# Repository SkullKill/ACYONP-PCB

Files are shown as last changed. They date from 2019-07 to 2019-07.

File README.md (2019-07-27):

# ACYONP-PCB
PCB for Access Control Yubikey OTP NFC Pi (ACYONP). For Raspberry Pi. This is a **Door Access Control using Electronic Door Strike, with Yubikey OTP via NFC / KeyPad / WebInterface for Authentication.**

Web interface shows the status of the whole system, along with the ability to enter pin/password/yubikey OTP string for authentication to unlock the door

Uses Inturrupt and Threads to minimise overhead, and to be non blocking as much as possible.

All options are completely customizable through the ini config file

The script [ACYONP](https://github.com/SkullKill/ACYONP) is design specificly for the Raspberry Pi.

SKaccess by Simon Kong

https://www.skaccess.com

ACYONP-SMD-01.jpg
NFC Reader is at the top of the Box, inside. putting the yubikey on top of the box will scan the yubikey neo / yubikey 5 nfc.


ACYONP-webinterface-01.jpg


## V 1.0 21/05/2019 - Initial Release

  ------------------------------------------------------------
## PCB Board Used

Ready to use PCB Board

https://www.skstore.com.au/electronics/pcb/ACYONP

PCB Design Files / gerber files

[ACYONP-PCB](https://github.com/SkullKill/ACYONP-PCB)

FYI Gerber files are in the release section

https://github.com/SkullKill/ACYONP-PCB/releases

more pictures in the wiki

https://github.com/SkullKill/ACYONP-PCB/wiki

ACYONP-SMD-Front-Red-RT-V1.2.jpg


ACYONP-SMD-Back-Red-V1.2.jpg


  ------------------------------------------------------------
## Schematics

ACYONP-SMD-schematics-v1.2a.jpg


------------------------------------------------------------
## Code Used

[ACYONP](https://github.com/SkullKill/ACYONP)

------------------------------------------------------------
## Product Used (not included)

### Dupont kit / Jumper Wires
you will need a dupont crimp kit 2.54 / tool
and / or jumper wires

e.g

Crimping Tool: 0.1-1.0 mm² Capacity, 16-28 AWG
https://www.pololu.com/product/1928

Crimp Connector Housings
https://www.pololu.com/category/70/crimp-connector-housings

Female Crimp Pins for 0.1" Housings
https://www.pololu.com/product/1930

Male Crimp Pins for 0.1" Housings
https://www.pololu.com/product/1931

Wires with Pre-Crimped Terminals
https://www.pololu.com/category/71/wires-with-pre-crimped-terminals

Premium Jumper Wires
https://www.pololu.com/category/65/premium-jumper-wires

https://www.futurlec.com/ConnHead.shtml

### Keypad

Metallic Waterproof 3x4 Keypad
https://www.futurlec.com/Keypads.shtml

### PN532 NFC controller in UART mode

e.g

https://www.dfrobot.com/product-892.html

https://wiki.dfrobot.com/NFC_Module_for_Arduino__SKU_DFR0231_

### Yubico Yubikey
YubiKey 5 NFC

https://www.yubico.com/product/yubikey-5-nfc

### other items used, can be any other ones.

H0307 • 145Lx105Wx65Dmm IP65 Sealed ABS Enclosure

https://www.altronics.com.au/p/h0307-ritec-145lx105wx65dmm-ip65-sealed-abs-enclosure/

H0151 • UB1 (157Lx95Wx53Hmm) Grey ABS Jiffy Box

https://www.altronics.com.au/p/h0151-ub1-157lx95wx53hmm-grey-abs-jiffy-box/

P0628 • 2.1mm Female Plastic Chassis Mount DC Power Socket (not necessary)

https://www.altronics.com.au/p/p0628-2.1mm-female-plastic-chassis-mount-dc-power-socket/

H1554 • 5mm LED Mounts Pk 100

https://www.altronics.com.au/p/h1554-5mm-led-mounts-pk-100/

S6109 • 1.5-24V Piezo Chassis Mount Buzzer (status buzzer)

https://www.altronics.com.au/p/s6109-1.5-24v-piezo-chassis-mount-buzzer/

S6100 • 3-15V Mechanical Chassis Mount Buzzer (door buzzer)

https://www.altronics.com.au/p/s6100-3-15v-mechanical-chassis-mount-buzzer/

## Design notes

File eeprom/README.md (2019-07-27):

https://github.com/raspberrypi/hats/tree/master/eepromutils

https://github.com/raspberrypi/linux/tree/rpi-4.19.y/arch/arm/boot/dts/overlays

https://www.stderr.nl/Blog/Hardware/RaspberryPi/PowerButton.html

https://lb.raspberrypi.org/forums/viewtopic.php?t=108134

vi /boot/config.txt
dtparam=i2c_vc=on

git clone https://github.com/raspberrypi/hats.git
sudo apt-get install device-tree-compiler

./eepmake eeprom_settings.txt acyonp_hat.eep

dd if=/dev/zero ibs=1k count=4 of=blank.eep

hexdump blank.eep

sudo ./eepflash.sh -w -f=blank.eep -t=24c32

sudo hexdump /sys/class/i2c-adapter/i2c-0/0-0050/eeprom

sudo ./eepflash.sh -w -f=acyonp_hat.eep -t=24c32

cat /proc/device-tree/hat/vendor
cat /proc/device-tree/hat/product

sudo sh -c 'echo "18" > /sys/class/gpio/export'
sudo sh -c 'echo "out" > /sys/class/gpio/gpio18/direction'
sudo sh -c 'echo "1" > /sys/class/gpio/gpio18/value'
sudo sh -c 'echo "0" > /sys/class/gpio/gpio18/value'

# compile dts overlay 
sudo dtc -@ -I dts -O dtb -o pi3-miniuart-bt-w1-gpio-overlay.dtb pi3-miniuart-bt-w1-gpio-overlay.dts ; sudo chown pi:pi pi3-miniuart-bt-w1-gpio-overlay.dtb

fdtdump pi3-miniuart-bt-w1-gpio-overlay.dtb

# generate eep with both board definition, and device-tree
./eepmake eeprom_settings.txt acyonp_hat-with-dt.eep pi3-miniuart-bt-w1-gpio-overlay.dtb

sudo ./eepflash.sh -w -f=blank.eep -t=24c32
sudo ./eepflash.sh -w -f=acyonp_hat-with-dt.eep -t=24c32

hexdump acyonp_hat-with-dt.eep
sudo hexdump /sys/class/i2c-adapter/i2c-0/0-0050/eeprom

To allow auto configuration after kernel boot (ie: modprobe some modules, TFT calibration, etc...), I use a custom parameter file, based on JSON, that could be parsed after. I choose JSON as it is small, human-readable, and easy to parse.
To add a custom file to your eep, just do this:
Code: Select all

./eepmake eeprom_settings.txt acyonp_hat-with-dt.eep myled.dtb -c myparams.json

cat /proc/device-tree/hat/product
cat /proc/device-tree/hat/product_id
cat /proc/device-tree/hat/product_ver
cat /proc/device-tree/hat/uuid
cat /proc/device-tree/hat/vendor

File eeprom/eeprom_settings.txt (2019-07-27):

########################################################################
# EEPROM settings text file
#
# Edit this file for your particular board and run through eepmake tool,
# then use eepflash tool to write to attached HAT ID EEPROM 
#
# Tools available:
#  eepmake   Parses EEPROM text file and creates binary .eep file
#  eepdump   Dumps a binary .eep file as human readable text (for debug)
#  eepflash  Write or read .eep binary image to/from HAT EEPROM
#
########################################################################

########################################################################
# Vendor info

# 128 bit UUID. If left at zero eepmake tool will auto-generate
# RFC 4122 compliant UUID
product_uuid 00000000-0000-0000-0000-000000000000

# 16 bit product id
product_id 0x0001

# 16 bit product version
product_ver 0x0001

# ASCII vendor string  (max 255 characters)
vendor "SKaccess"

# ASCII product string (max 255 characters)
product "ACYONP - Access Control Yubikey OTP NFC Pi"

########################################################################
# GPIO bank settings, set to nonzero to change from the default.
# NOTE these setting can only be set per BANK, uncommenting any of
# these will force the bank to use the custom setting.

# drive strength, 0=default, 1-8=2,4,6,8,10,12,14,16mA, 9-15=reserved
gpio_drive 0

# 0=default, 1=slew rate limiting, 2=no slew limiting, 3=reserved
gpio_slew 0

# 0=default, 1=hysteresis disabled, 2=hysteresis enabled, 3=reserved
gpio_hysteresis 0

# If board back-powers Pi via 5V GPIO header pins:
# 0 = board does not back-power
# 1 = board back-powers and can supply the Pi with a minimum of 1.3A
# 2 = board back-powers and can supply the Pi with a minimum of 2A
# 3 = reserved
# If back_power=2 then USB high current mode will be automatically 
# enabled on the Pi
back_power 2

########################################################################
# GPIO pins, uncomment for GPIOs used on board
# Options for FUNCTION: INPUT, OUTPUT, ALT0-ALT5
# Options for PULL: DEFAULT, UP, DOWN, NONE
# NB GPIO0 and GPIO1 are reserved for ID EEPROM so cannot be set

#         GPIO  FUNCTION  PULL
#         ----  --------  ----
#setgpio  2     INPUT     DEFAULT
#setgpio  3     INPUT     DEFAULT
#setgpio  4     INPUT     DEFAULT
#setgpio  5     INPUT     DEFAULT
#setgpio  6     INPUT     DEFAULT
#setgpio  7     INPUT     DEFAULT
#setgpio  8     INPUT     DEFAULT
#setgpio  9     INPUT     DEFAULT
#setgpio  10    INPUT     DEFAULT
#setgpio  11    INPUT     DEFAULT
#setgpio  12    INPUT     DEFAULT
#setgpio  13    INPUT     DEFAULT
#setgpio  14    INPUT     DEFAULT
#setgpio  15    INPUT     DEFAULT
#setgpio  16    INPUT     DEFAULT
#setgpio  17    INPUT     DEFAULT
#setgpio  18    INPUT     DEFAULT
#setgpio  19    INPUT     DEFAULT
#setgpio  20    INPUT     DEFAULT
#setgpio  21    INPUT     DEFAULT
#setgpio  22    INPUT     DEFAULT
#setgpio  23    INPUT     DEFAULT
#setgpio  24    INPUT     DEFAULT
#setgpio  25    INPUT     DEFAULT
#setgpio  26    INPUT     DEFAULT
#setgpio  27    INPUT     DEFAULT

#         GPIO  FUNCTION  PULL
#         ----  --------  ----
# unused / KeyPad Col 4 / i2c SDA
#setgpio  2     INPUT     DEFAULT
# Relay 4 / i2c SCL
#setgpio  3     OUTPUT     DOWN
# 1-wire
#setgpio  4     INPUT     DEFAULT
# Power to Solenoid strike input
setgpio  5     INPUT     UP
# Latch Open input
setgpio  6     INPUT     UP
# Relay 3
setgpio  7     OUTPUT     DOWN
# Relay 2 Door Buzzer
setgpio  8     OUTPUT     DOWN
# KeyPad Col 3
setgpio  9     OUTPUT     DOWN
# KeyPad Col 2
setgpio  10    OUTPUT     DOWN
# Relay 1 Door Strike
setgpio  11    OUTPUT     DOWN
# Reed Switch Open input
setgpio  12    INPUT     UP
# DoorOpen Button
setgpio  13    INPUT     UP
# To NFC TX
setgpio  14    ALT0     DEFAULT
# to NFC RX
setgpio  15    ALT0     DEFAULT
# Latch Open LED
setgpio  16    OUTPUT     DOWN
# KeyPad Row 1
setgpio  17    INPUT     UP
# PWM status buzzer (active, not passive, so no PWM used)
setgpio  18    OUTPUT     DOWN
# Power to Solenoid Strike LED
setgpio  19    OUTPUT     DOWN
# Alarm LED
setgpio  20    OUTPUT     DOWN
# Status LED
setgpio  21    OUTPUT     DOWN
# KeyPad Row 3
setgpio  22    INPUT     UP
# KeyPad Row 4
setgpio  23    INPUT     UP
# KeyPad Col 1
setgpio  24    OUTPUT     DOWN
# NFC PowerSwitch
setgpio  25    OUTPUT     DOWN
# Reed Switch open LED
setgpio  26    OUTPUT     DOWN
# KeyPad Row 2
setgpio  27    INPUT     UP

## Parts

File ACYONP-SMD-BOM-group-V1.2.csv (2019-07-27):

Reference | Quantity | Value | Footprint | Datasheet | LCSC | LCSCweb | ALT | MPN | Alt | MPNweb | web
C2 C5 C3 C6 | 4 | 100nF-25V | Capacitor_SMD:C_0805_2012Metric_Pad1.15x1.40mm_HandSolder | https://datasheet.lcsc.com/szlcsc/Murata-Electronics-GRM21BR71E104KA01L_C86041.pdf | C86041 | https://lcsc.com/product-detail/Multilayer-Ceramic-Capacitors-MLCC-SMD-SMT_MuRata_GRM21BR71E104KA01L_100nF-104-10-25V_C86041.html |  | GRM21BR71E104KA01L
C4 C1 C7 | 3 | 22UF-25V | Capacitor_SMD:C_0805_2012Metric_Pad1.15x1.40mm_HandSolder | https://datasheet.lcsc.com/szlcsc/Samsung-Electro-Mechanics-CL21A226MAQNNNE_C45783.pdf | C45783 | https://lcsc.com/product-detail/Multilayer-Ceramic-Capacitors-MLCC-SMD-SMT_SAMSUNG_CL21A226MAQNNNE_22uF-226-20-25V_C45783.html | C86816 | CL21A226MAQNNNE
D1 D10 D9 D2 | 4 | SOD1F7 | Diode_SMD:D_SOD-123 | https://datasheet.lcsc.com/szlcsc/1903041730_MDD-Jiangsu-Yutai-Elec-SOD1F7_C33221.pdf | C33221 | https://lcsc.com/product-detail/Diodes-Rectifiers-Fast-Recovery_Jiangsu-Yutai-Elec-SOD1F7_C33221.html |  | SOD1F7
D3 D4 D11 D12 D13 D14 D15 | 7 | LED-Green | LED_SMD:LED_0805_2012Metric_Pad1.15x1.40mm_HandSolder | https://datasheet.lcsc.com/szlcsc/Foshan-NationStar-Optoelectronics-FC-2012UGK-520D5_C84260.pdf | C84260 | https://lcsc.com/product-detail/Light-Emitting-Diodes-LED_Emerald-SMDLED-Iv-220-270mcd-atIF-5mA_C84260.html |  | FC-2012UGK-520D5
D5 D6 | 2 | LED-Yellow | LED_SMD:LED_0805_2012Metric_Pad1.15x1.40mm_HandSolder | https://datasheet.lcsc.com/szlcsc/Foshan-NationStar-Optoelectronics-FC-2012HYK-588J_C84261.pdf | C84261 | https://lcsc.com/product-detail/Light-Emitting-Diodes-LED_Yellow-light-SMDLED-105-125mcd_C84261.html |  | FC-2012HYK-588J
D7 | 1 | LED-Red | LED_SMD:LED_0805_2012Metric_Pad1.15x1.40mm_HandSolder | https://datasheet.lcsc.com/szlcsc/Foshan-NationStar-Optoelectronics-FC-2012HRK-620D_C84256.pdf | C84256 | https://lcsc.com/product-detail/Light-Emitting-Diodes-LED_Red-LED-SMDLED-80-180mcd_C84256.html |  | FC-2012HRK-620D
D8 | 1 | LED-Blue | LED_SMD:LED_0805_2012Metric_Pad1.15x1.40mm_HandSolder | https://datasheet.lcsc.com/szlcsc/Foshan-NationStar-Optoelectronics-FC-A2012BK-470H2_C84259.pdf | C84259 | https://lcsc.com/product-detail/Light-Emitting-Diodes-LED_Blue-light-SMDLED-36-45mcdat2mA_C84259.html |  | FC-A2012BK-470H2
F1 | 1 | PTC-2A-16V_1812 | Fuse:Fuse_1812_4532Metric_Pad1.30x3.40mm_HandSolder | https://datasheet.lcsc.com/szlcsc/SOCAY-Elec-SCF200-16-1812R_C305617.pdf | C305617 | https://lcsc.com/product-detail/Others_SOCAY-Elec-SCF200-16-1812R_C305617.html |  | SCF200-16-1812R
J1 | 1 | Raspberry_Pi_2_3 | Connector_PinSocket_2.54mm:PinSocket_2x20_P2.54mm_Vertical | https://www.raspberrypi.org/documentation/hardware/raspberrypi/schematics/rpi_SCH_3bplus_1p0_reduced.pdf | C50982 | https://lcsc.com/product-detail/Pin-Header-Female-Header_Boom-Precision-Elec-2-54mm-2-20PFemale-header_C50982.html |  |  | C35165
J12 | 1 | 1-Wire | Connector_PinHeader_2.54mm:PinHeader_1x03_P2.54mm_Vertical | https://datasheet.lcsc.com/szlcsc/Boom-Precision-Elec-Header-2-54mm-1-3P_C49257.pdf | C49257 | https://lcsc.com/product-detail/Pin-Header-Female-Header_Boom-Precision-Elec-Header-2-54mm-1-3P_C49257.html
J15 | 1 | NFC_Module | Connector_PinHeader_2.54mm:PinHeader_1x04_P2.54mm_Vertical | https://datasheet.lcsc.com/szlcsc/Shenzhen-Cankemeng-Headers-Pins-1-4P-2-54mm-Straight-line_C124378.pdf | C124378 | https://lcsc.com/product-detail/Pin-Header-Female-Header_Shenzhen-Cankemeng-Headers-Pins-1-4P-2-54mm-Straight-line_C124378.html
J16 | 1 | 12Vpsu | TerminalBlock:TerminalBlock_bornier-2_P5.08mm | https://datasheet.lcsc.com/szlcsc/Ningbo-Kangnex-Elec-WJ126V-5-0-2P_C8404.pdf | C8404 | https://lcsc.com/product-detail/Pluggable-System-Terminal-Block_Ningbo-Kangnex-Elec-WJ126V-5-0-2P_C8404.html |  | WJ126V-5.0-2P
J18 | 1 | LatchOpen | Connector_PinHeader_2.54mm:PinHeader_1x02_P2.54mm_Vertical | ~ | C124375
J19 | 1 | ReedSwitchOpen | Connector_PinHeader_2.54mm:PinHeader_1x02_P2.54mm_Vertical | ~ | C124375
J20 | 1 | AlarmStatus | Connector_PinHeader_2.54mm:PinHeader_1x02_P2.54mm_Vertical | ~ | C124375
J21 | 1 | PowerStatus | Connector_PinHeader_2.54mm:PinHeader_1x02_P2.54mm_Vertical | ~ | C124375
J22 | 1 | ProgrammingJumper | Connector_PinHeader_2.54mm:PinHeader_1x02_P2.54mm_Vertical | ~ | C124375
J23 | 1 | Screw_Terminal_01x04_Left_Top | TerminalBlock_TE-Connectivity:TerminalBlock_TE_282834-4_1x04_P2.54mm_Horizontal | ~ |  |  |  | KF128-2.54-4P |  | http://en.cnkefa.com/index.php?c=product&id=159 | https://www.aliexpress.com/store/group/Connection-terminal/4657016_515213135.html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
J24 | 1 | Screw_Terminal_01x04_Left_Bottom | TerminalBlock_TE-Connectivity:TerminalBlock_TE_282834-4_1x04_P2.54mm_Horizontal | ~ |  |  |  | KF128-2.54-4P |  | http://en.cnkefa.com/index.php?c=product&id=159 | https://www.aliexpress.com/store/group/Connection-terminal/4657016_515213135.html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
J25 | 1 | Screw_Terminal_01x08_Bottom_Left | TerminalBlock_TE-Connectivity:TerminalBlock_TE_282834-8_1x08_P2.54mm_Horizontal | ~ |  |  |  | KF128-2.54-8P |  | http://en.cnkefa.com/index.php?c=product&id=159
J26 | 1 | Screw_Terminal_01x06_Top_Right | TerminalBlock_TE-Connectivity:TerminalBlock_TE_282834-6_1x06_P2.54mm_Horizontal | ~ |  |  |  | KF128-2.54-6P |  | http://en.cnkefa.com/index.php?c=product&id=159
J5 | 1 | PowerToSolenoidStrike | Connector_PinHeader_2.54mm:PinHeader_1x02_P2.54mm_Vertical | https://datasheet.lcsc.com/szlcsc/Shenzhen-Cankemeng-Headers-Pins-1-2P-2-54mm-Straight-line_C124375.pdf | C124375 | https://lcsc.com/product-detail/Pin-Header-Female-Header_Shenzhen-Cankemeng-Headers-Pins-1-2P-2-54mm-Straight-line_C124375.html
J8 | 1 | KeyPad3X4 | Connector_PinHeader_2.54mm:PinHeader_1x08_P2.54mm_Vertical | https://datasheet.lcsc.com/szlcsc/Shenzhen-Cankemeng-Headers-Pins-1-8P-2-54mm-Straight-line_C124381.pdf | C124381 | https://lcsc.com/product-detail/Pin-Header-Female-Header_Shenzhen-Cankemeng-Headers-Pins-1-8P-2-54mm-Straight-line_C124381.html
J9 | 1 | I2C | Connector_PinHeader_2.54mm:PinHeader_1x02_P2.54mm_Vertical | ~ | C124375
JP1 | 1 | 5V-3.3V Sw NFC | Connector_PinHeader_2.54mm:PinHeader_1x03_P2.54mm_Vertical | https://datasheet.lcsc.com/szlcsc/Boom-Precision-Elec-Header-2-54mm-1-3P_C49257.pdf | C49257 | https://lcsc.com/product-detail/Pin-Header-Female-Header_Boom-Precision-Elec-Header-2-54mm-1-3P_C49257.html
JP2 | 1 | 5V-12V Jumper | Connector_PinHeader_2.54mm:PinHeader_1x03_P2.54mm_Vertical | https://datasheet.lcsc.com/szlcsc/Boom-Precision-Elec-Header-2-54mm-1-3P_C49257.pdf | C49257 | https://lcsc.com/product-detail/Pin-Header-Female-Header_Boom-Precision-Elec-Header-2-54mm-1-3P_C49257.html
L1 | 1 | 3.3UH-8.5A | ACYONP-SMD-LCSC:L_6.3x6.3_H3_HandSolder | https://datasheet.lcsc.com/szlcsc/1812181433_MAZO-MPCA-0630-3R3-M_C268402.pdf | C268402 | https://lcsc.com/product-detail/Others_MAZO-MPCA-0630-3R3-M_C268402.html | C207839 | MPCA-0630-3R3-M
Q11 | 1 | DMMT5401 | Package_TO_SOT_SMD:SOT-23-6 | https://datasheet.lcsc.com/szlcsc/Diodes-Incorporated-DMMT5401-7-F_C154733.pdf | C154733 | https://lcsc.com/product-detail/Transistors-NPN-PNP_DIODES_DMMT5401-7-F_DMMT5401-7-F_C154733.html |  | DMMT5401-7-F
Q12 Q1 | 2 | DMG2305UX | Package_TO_SOT_SMD:SOT-23 | https://datasheet.lcsc.com/szlcsc/Diodes-Incorporated-DMG2305UX-13_C144153.pdf | C144153 | https://lcsc.com/product-detail/MOSFET_Diodes-Incorporated_DMG2305UX-13_Diodes-Incorporated-DMG2305UX-13_C144153.html |  | DMG2305UX-13
Q3 Q5 Q7 Q9 Q2 | 5 | FMMT491TA | Package_TO_SOT_SMD:SOT-23 | https://datasheet.lcsc.com/szlcsc/1811291034_Diodes-Incorporated-FMMT491TA_C141788.pdf | C141788 | https://lcsc.com/product-detail/Transistors-NPN-PNP_Diodes-Incorporated_FMMT491TA_Diodes-Incorporated-FMMT491TA_C141788.html |  | FMMT491TA
R1 R6 R10 R14 | 4 | 2KΩ | Resistor_SMD:R_0805_2012Metric_Pad1.15x1.40mm_HandSolder | https://datasheet.lcsc.com/szlcsc/YAGEO-RC0805FR-072KL_C114572.pdf | C114572 | https://lcsc.com/product-detail/Chip-Resistor-Surface-Mount_2KR-2001-0-5_C114572.html |  | RC0805FR-072KL
R15 | 1 | 47KΩ | Resistor_SMD:R_0805_2012Metric_Pad1.15x1.40mm_HandSolder | https://datasheet.lcsc.com/szlcsc/YAGEO-RC0805FR-0747KL_C126351.pdf | C126351 | https://lcsc.com/product-detail/Chip-Resistor-Surface-Mount_47KR-4702-1_C126351.html |  | RC0805FR-0747KL
R19 | 1 | 1KΩ | Resistor_SMD:R_0805_2012Metric_Pad1.15x1.40mm_HandSolder | https://datasheet.lcsc.com/szlcsc/YAGEO-RC0805FR-071KL_C95781.pdf | C95781 | https://lcsc.com/product-detail/Chip-Resistor-Surface-Mount_1KR-1000-1_C95781.html |  | RC0805FR-071KL
R21 R23 R24 | 3 | 4.7KΩ | Resistor_SMD:R_0805_2012Metric_Pad1.15x1.40mm_HandSolder | https://datasheet.lcsc.com/szlcsc/YAGEO-RC0805FR-074K7L_C60816.pdf | C60816 | https://lcsc.com/product-detail/Chip-Resistor-Surface-Mount_4-7K-4701-1_C60816.html |  | RC0805FR-074K7L
R22 R28 | 2 | 3.9KΩ | Resistor_SMD:R_0805_2012Metric_Pad1.15x1.40mm_HandSolder | https://datasheet.lcsc.com/szlcsc/YAGEO-RC0805FR-073K9L_C114221.pdf | C114221 | https://lcsc.com/product-detail/Chip-Resistor-Surface-Mount_3-9KR-3901-1_C114221.html |  | RC0805FR-073K9L
R26 | 1 | 57.6KΩ | Resistor_SMD:R_0805_2012Metric_Pad1.15x1.40mm_HandSolder | https://datasheet.lcsc.com/szlcsc/YAGEO-RC0805FR-0757K6L_C163405.pdf | C163405 | https://lcsc.com/product-detail/Chip-Resistor-Surface-Mount_RC0805FR-0757K6L_C163405.html |  | RC0805FR-0757K6L
R29 R30 R31 R33 R32 R27 R18 | 7 | 330Ω | Resistor_SMD:R_0805_2012Metric_Pad1.15x1.40mm_HandSolder | https://datasheet.lcsc.com/szlcsc/YAGEO-RC0805FR-07330RL_C105878.pdf | C105878 | https://lcsc.com/product-detail/Chip-Resistor-Surface-Mount_330R-330R-1_C105878.html |  | RC0805FR-07330RL
R3 R8 R12 R16 R20 | 5 | 150Ω | Resistor_SMD:R_0805_2012Metric_Pad1.15x1.40mm_HandSolder | https://datasheet.lcsc.com/szlcsc/YAGEO-RC0805FR-07150RL_C114523.pdf | C114523 | https://lcsc.com/product-detail/Chip-Resistor-Surface-Mount_150R-1500-1_C114523.html | C228315 | RC0805FR-07150RL
R4 R25 R11 | 3 | 10KΩ | Resistor_SMD:R_0805_2012Metric_Pad1.15x1.40mm_HandSolder | https://datasheet.lcsc.com/szlcsc/YAGEO-RC0805DR-0710KL_C163503.pdf | C163503 | https://lcsc.com/product-detail/Chip-Resistor-Surface-Mount_10KR-1002-0-5_C163503.html |  | RC0805DR-0710KL
R5 R17 R2 | 3 | 510Ω | Resistor_SMD:R_0805_2012Metric_Pad1.15x1.40mm_HandSolder | https://datasheet.lcsc.com/szlcsc/YAGEO-RC0805FR-07510RL_C114563.pdf | C114563 | https://lcsc.com/product-detail/Chip-Resistor-Surface-Mount_510R-510R-1_C114563.html |  | RC0805FR-07510RL
R7 | 1 | 1.2KΩ | Resistor_SMD:R_0805_2012Metric_Pad1.15x1.40mm_HandSolder | https://datasheet.lcsc.com/szlcsc/YAGEO-RC0805FR-071K2L_C114526.pdf | C114526 | https://lcsc.com/product-detail/Chip-Resistor-Surface-Mount_1-2KR-1201-1_C114526.html |  | RC0805FR-071K2L
R9 R13 | 2 | 270Ω | Resistor_SMD:R_0805_2012Metric_Pad1.15x1.40mm_HandSolder | https://datasheet.lcsc.com/szlcsc/YAGEO-RC0805FR-07270RL_C137558.pdf | C137558 | https://lcsc.com/product-detail/Chip-Resistor-Surface-Mount_270R-270R-1_C137558.html |  | RC0805FR-07270RL
SW1 | 1 | 5V Reg Sw on-off | Button_Switch_SMD:SW_SPDT_PCM12 | https://datasheet.lcsc.com/szlcsc/Korean-Hroparts-Elec-K3-1292S-P2_C145853.pdf | C145853 | https://lcsc.com/product-detail/Toggle-Switches_Korean-Hroparts-Elec-K3-1292S-P2_C145853.html |  | K3-1292S-P2
U1 | 1 | TPS563200 | Package_TO_SOT_SMD:SOT-23-6_Handsoldering | http://www.ti.com/lit/ds/symlink/tps563200.pdf | C97253 | https://lcsc.com/product-detail/DC-DC-Converters_TI_TPS563200DDCR_TPS563200DDCR_C97253.html |  | TPS563200DDCR
U2 | 1 | CAT24C32 | Package_SO:SOIC-8_3.9x4.9mm_P1.27mm | https://datasheet.lcsc.com/szlcsc/ON-Semicon-ON-CAT24C32WI-GT3_C81193.pdf | C81193 | https://lcsc.com/product-detail/EEPROM_ON-Semicon_CAT24C32WI-GT3_ON-Semicon-ON-CAT24C32WI-GT3_C81193.html |  | CAT24C32WI-GT3
U3 | 1 | ULN2003A | ACYONP-SMD-LCSC:SOIC-16_ti-Package-D | https://datasheet.lcsc.com/szlcsc/Texas-Instruments-TI-ULN2003ADR_C7512.pdf | C7512 | https://lcsc.com/product-detail/Darlington-transistor-array-driver_Texas-Instruments_ULN2003ADR_Texas-Instruments-TI-ULN2003ADR_C7512.html |  | ULN2003ADR

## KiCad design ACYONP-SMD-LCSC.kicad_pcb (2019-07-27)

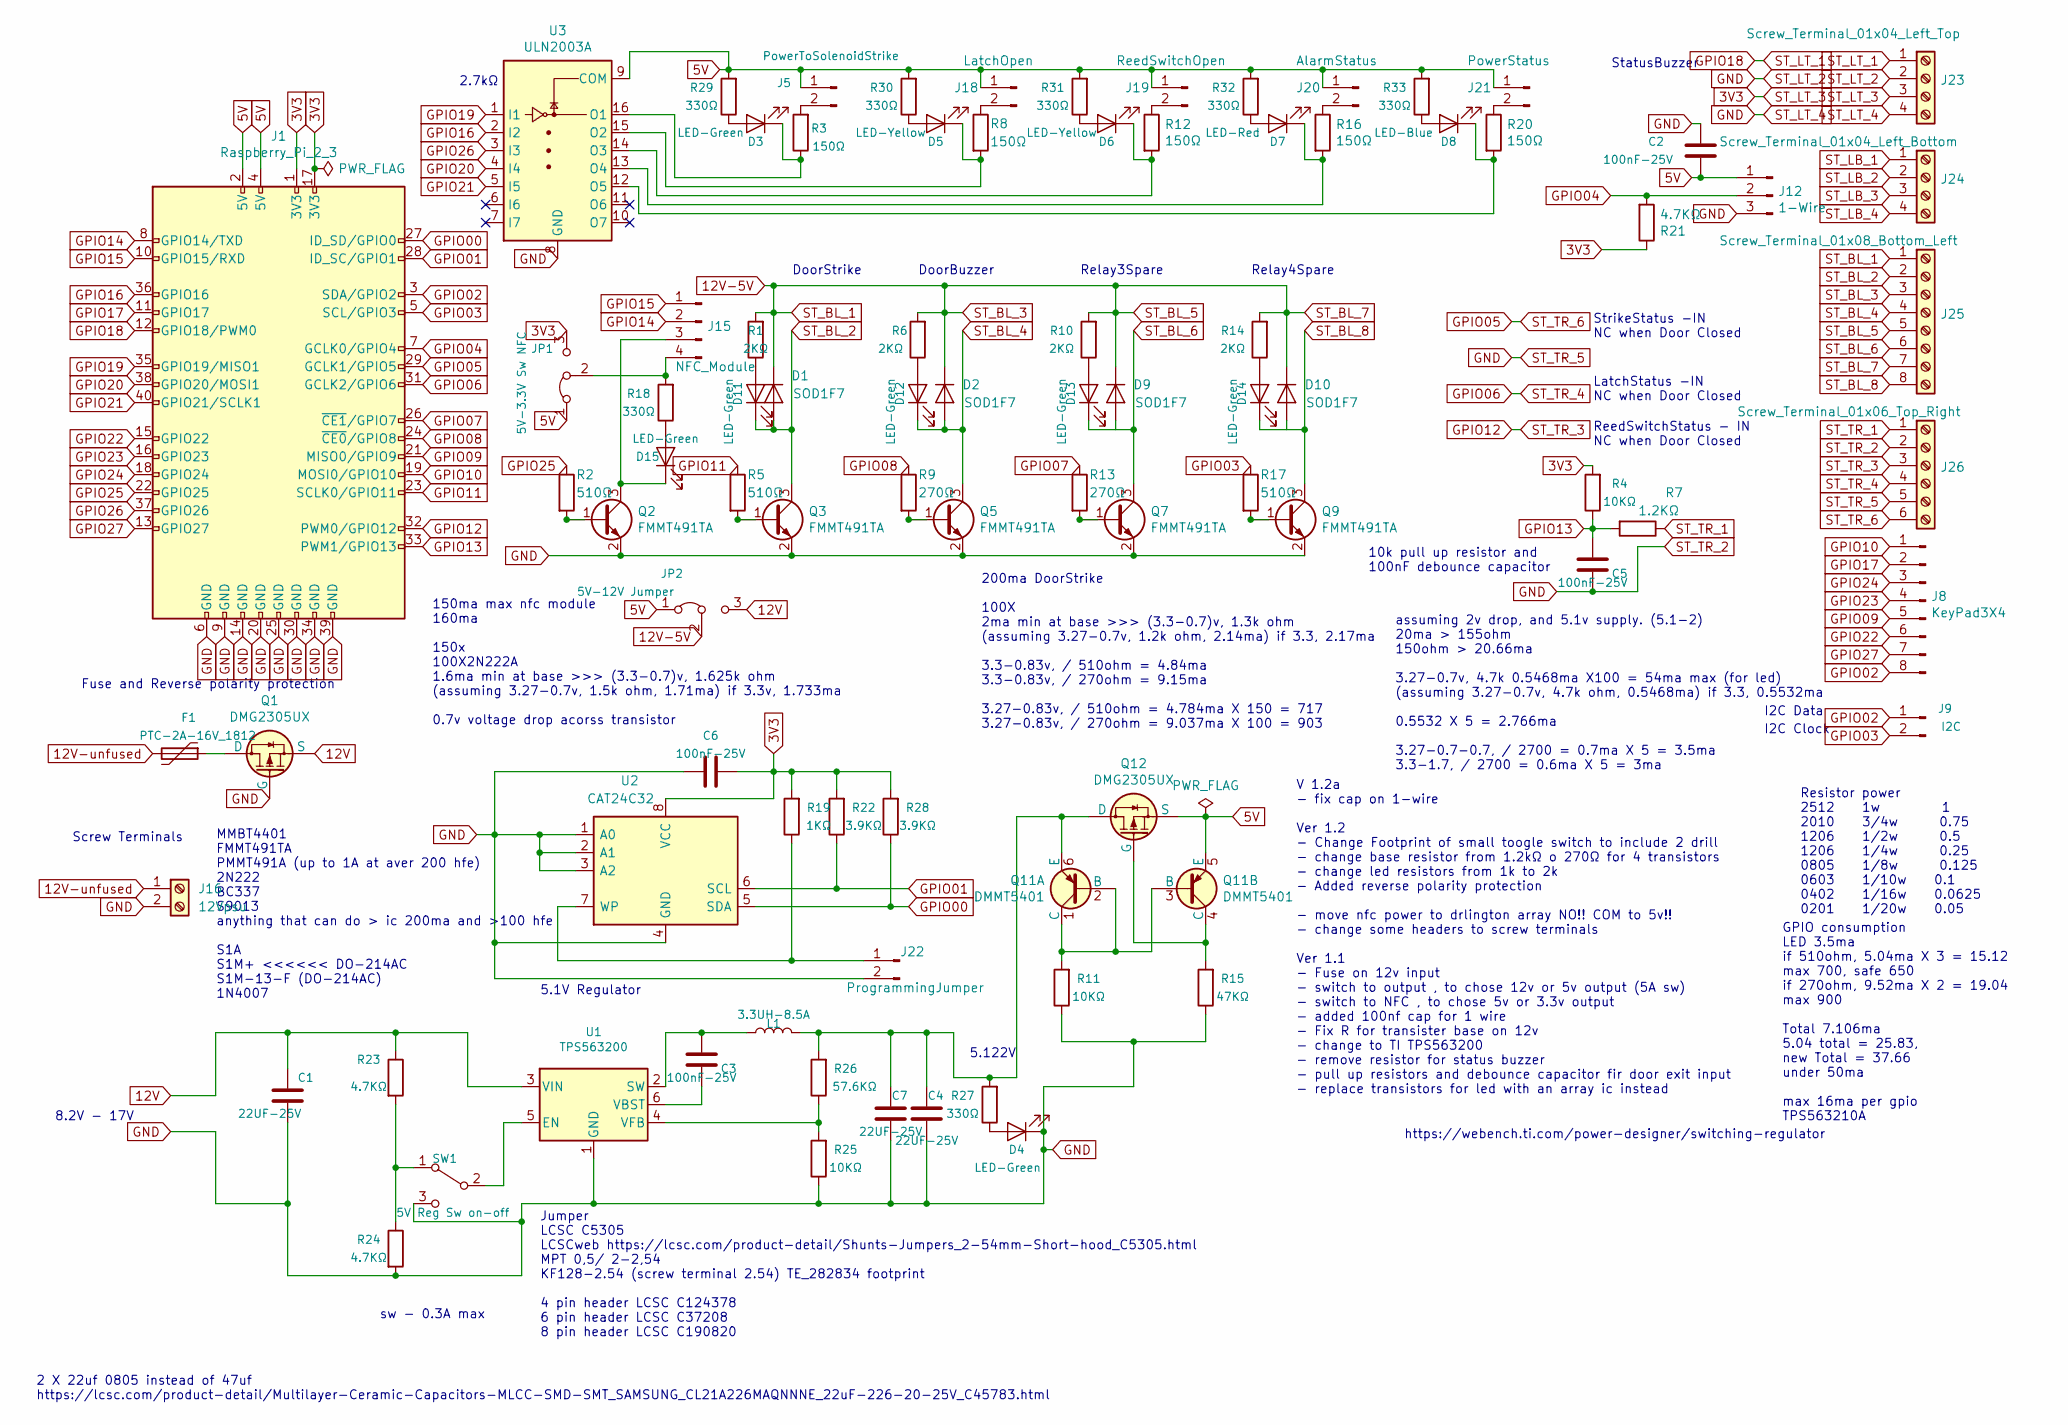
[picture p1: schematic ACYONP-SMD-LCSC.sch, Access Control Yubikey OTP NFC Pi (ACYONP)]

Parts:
C1, C4, C7: 22UF-25V; C_0805_2012Metric_Pad1.15x1.40mm_HandSolder; MPN CL21A226MAQNNNE; LCSC C45783
C2, C3, C5, C6: 100nF-25V; C_0805_2012Metric_Pad1.15x1.40mm_HandSolder; MPN GRM21BR71E104KA01L; LCSC C86041
D1, D9, D10: SOD1F7; D_SOD-123; MPN SOD1F7; LCSC C33221
D2: SOD1F7; D_SOD-123
D3, D4, D11, D12, D13, D14, D15: LED-Green; LED_0805_2012Metric_Pad1.15x1.40mm_HandSolder; MPN FC-2012UGK-520D5; LCSC C84260
D5, D6: LED-Yellow; LED_0805_2012Metric_Pad1.15x1.40mm_HandSolder; MPN FC-2012HYK-588J; LCSC C84261
D7: LED-Red; LED_0805_2012Metric_Pad1.15x1.40mm_HandSolder; MPN FC-2012HRK-620D; LCSC C84256
D8: LED-Blue; LED_0805_2012Metric_Pad1.15x1.40mm_HandSolder; MPN FC-A2012BK-470H2; LCSC C84259
F1: PTC-2A-16V_1812; Fuse_1812_4532Metric_Pad1.30x3.40mm_HandSolder; MPN SCF200-16-1812R; LCSC C305617
J1: Raspberry_Pi_2_3; PinSocket_2x20_P2.54mm_Vertical; LCSC C50982
J5: PowerToSolenoidStrike; PinHeader_1x02_P2.54mm_Vertical; LCSC C124375
J8: KeyPad3X4; PinHeader_1x08_P2.54mm_Vertical; LCSC C124381
J9: I2C; PinHeader_1x02_P2.54mm_Vertical; LCSC C124375
J12: 1-Wire; PinHeader_1x03_P2.54mm_Vertical; LCSC C49257
J15: NFC_Module; PinHeader_1x04_P2.54mm_Vertical; LCSC C124378
J16: 12Vpsu; TerminalBlock_bornier-2_P5.08mm; MPN WJ126V-5.0-2P; LCSC C8404
J18: LatchOpen; PinHeader_1x02_P2.54mm_Vertical; LCSC C124375
J19: ReedSwitchOpen; PinHeader_1x02_P2.54mm_Vertical; LCSC C124375
J20: AlarmStatus; PinHeader_1x02_P2.54mm_Vertical; LCSC C124375
J21: PowerStatus; PinHeader_1x02_P2.54mm_Vertical; LCSC C124375
J22: ProgrammingJumper; PinHeader_1x02_P2.54mm_Vertical; LCSC C124375
J23: Screw_Terminal_01x04_Left_Top; TerminalBlock_TE_282834-4_1x04_P2.54mm_Horizontal; MPN KF128-2.54-4P
J24: Screw_Terminal_01x04_Left_Bottom; TerminalBlock_TE_282834-4_1x04_P2.54mm_Horizontal; MPN KF128-2.54-4P
J25: Screw_Terminal_01x08_Bottom_Left; TerminalBlock_TE_282834-8_1x08_P2.54mm_Horizontal; MPN KF128-2.54-8P
J26: Screw_Terminal_01x06_Top_Right; TerminalBlock_TE_282834-6_1x06_P2.54mm_Horizontal; MPN KF128-2.54-6P
JP1: 5V-3.3V Sw NFC; PinHeader_1x03_P2.54mm_Vertical; LCSC C49257
JP2: 5V-12V Jumper; PinHeader_1x03_P2.54mm_Vertical; LCSC C49257
L1: 3.3UH-8.5A; L_6.3x6.3_H3_HandSolder; MPN MPCA-0630-3R3-M; LCSC C268402
Q1, Q12: DMG2305UX; SOT-23; MPN DMG2305UX-13; LCSC C144153
Q2, Q3: FMMT491TA; SOT-23; MPN FMMT491TA; LCSC C141788
Q5, Q7, Q9: FMMT491TA; SOT-23
Q11: DMMT5401; SOT-23-6; MPN DMMT5401-7-F; LCSC C154733
R1, R6, R10, R14: 2KΩ; R_0805_2012Metric_Pad1.15x1.40mm_HandSolder; MPN RC0805FR-072KL; LCSC C114572
R2, R5: 510Ω; R_0805_2012Metric_Pad1.15x1.40mm_HandSolder; MPN RC0805FR-07510RL; LCSC C114563
R3: 150Ω; R_0805_2012Metric_Pad1.15x1.40mm_HandSolder; MPN RC0805FR-07150RL; LCSC C114523
R4, R11, R25: 10KΩ; R_0805_2012Metric_Pad1.15x1.40mm_HandSolder; MPN RC0805DR-0710KL; LCSC C163503
R7: 1.2KΩ; R_0805_2012Metric_Pad1.15x1.40mm_HandSolder; MPN RC0805FR-071K2L; LCSC C114526
R8, R12, R16, R20: 150Ω; R_0805_2012Metric_Pad1.15x1.40mm_HandSolder
R9: 270Ω; R_0805_2012Metric_Pad1.15x1.40mm_HandSolder; MPN RC0805FR-07270RL; LCSC C137558
R13: 270Ω; R_0805_2012Metric_Pad1.15x1.40mm_HandSolder
R15: 47KΩ; R_0805_2012Metric_Pad1.15x1.40mm_HandSolder; MPN RC0805FR-0747KL; LCSC C126351
R17: 510Ω; R_0805_2012Metric_Pad1.15x1.40mm_HandSolder
R18, R27, R29, R30, R31, R32, R33: 330Ω; R_0805_2012Metric_Pad1.15x1.40mm_HandSolder; MPN RC0805FR-07330RL; LCSC C105878
R19: 1KΩ; R_0805_2012Metric_Pad1.15x1.40mm_HandSolder; MPN RC0805FR-071KL; LCSC C95781
R21: 4.7KΩ; R_0805_2012Metric_Pad1.15x1.40mm_HandSolder; MPN RC0805FR-074K7L; LCSC C60816
R22, R28: 3.9KΩ; R_0805_2012Metric_Pad1.15x1.40mm_HandSolder; MPN RC0805FR-073K9L; LCSC C114221
R23, R24: 4.7KΩ; R_0805_2012Metric_Pad1.15x1.40mm_HandSolder
R26: 57.6KΩ; R_0805_2012Metric_Pad1.15x1.40mm_HandSolder; MPN RC0805FR-0757K6L; LCSC C163405
SW1: 5V Reg Sw on-off; SW_SPDT_PCM12; MPN K3-1292S-P2; LCSC C145853
U1: TPS563200; SOT-23-6_Handsoldering; MPN TPS563200DDCR; LCSC C97253
U2: CAT24C32; SOIC-8_3.9x4.9mm_P1.27mm; MPN CAT24C32WI-GT3; LCSC C81193
U3: ULN2003A; SOIC-16_ti-Package-D; MPN ULN2003ADR; LCSC C7512

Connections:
3V3: C6.2, J1.1 (3V3), J1.17 (3V3), J23.3, JP1.3 (B), R4.2, R19.2, R21.1, R22.2, R28.2, U2.8 (VCC)
5V: C2.1, J1.2 (5V), J1.4 (5V), J5.1, J12.1, J18.1, J19.1, J20.1, J21.1, JP1.1 (A), JP2.1 (A), Q11.5 (E), Q12.2 (S), R29.2, R30.2, R31.2, R32.2, R33.2, U3.9 (COM)
12V: C1.2, JP2.3 (B), Q1.2 (S), R23.1, U1.3 (VIN)
12V-5V: D1.1 (K), D2.1 (K), D9.1 (K), D10.1 (K), J25.1, J25.3, J25.5, J25.7, JP2.2 (C), R1.2, R6.2, R10.2, R14.2
12V-unfused: F1.2, J16.1
GND: C1.1, C2.2, C4.2, C5.2, C6.1, C7.2, D4.1 (K), J1.6 (GND), J1.9 (GND), J1.14 (GND), J1.20 (GND), J1.25 (GND), J1.30 (GND), J1.34 (GND), J1.39 (GND), J12.3, J16.2, J22.2, J23.2, J23.4, J26.2, J26.5, Q1.1 (G), Q2.2 (E), Q3.2 (E), Q5.2 (E), Q7.2 (E), Q9.2 (E), R11.1, R15.1, R24.2, R25.1, SW1.3 (C), U1.1 (GND), U2.1 (A0), U2.2 (A1), U2.3 (A2), U2.4 (GND), U3.8 (GND)
GPIO00: J1.27 (ID_SD/GPIO0), R28.1, U2.5 (SDA)
GPIO01: J1.28 (ID_SC/GPIO1), R22.1, U2.6 (SCL)
GPIO02: J1.3 (SDA/GPIO2), J8.8, J9.1
GPIO03: J1.5 (SCL/GPIO3), J9.2, R17.1
GPIO04: J1.7 (GCLK0/GPIO4), J12.2, R21.2
GPIO05: J1.29 (GCLK1/GPIO5), J26.6
GPIO06: J1.31 (GCLK2/GPIO6), J26.4
GPIO07: J1.26 (~CE1~/GPIO7), R13.1
GPIO08: J1.24 (~CE0~/GPIO8), R9.1
GPIO09: J1.21 (MISO0/GPIO9), J8.5
GPIO10: J1.19 (MOSI0/GPIO10), J8.1
GPIO11: J1.23 (SCLK0/GPIO11), R5.1
GPIO12: J1.32 (PWM0/GPIO12), J26.3
GPIO13: C5.1, J1.33 (PWM1/GPIO13), R4.1, R7.2
GPIO14: J1.8 (GPIO14/TXD), J15.2
GPIO15: J1.10 (GPIO15/RXD), J15.1
GPIO16: J1.36 (GPIO16), U3.2 (I2)
GPIO17: J1.11 (GPIO17), J8.2
GPIO18: J1.12 (GPIO18/PWM0), J23.1
GPIO19: J1.35 (GPIO19/MISO1), U3.1 (I1)
GPIO20: J1.38 (GPIO20/MOSI1), U3.4 (I4)
GPIO21: J1.40 (GPIO21/SCLK1), U3.5 (I5)
GPIO22: J1.15 (GPIO22), J8.6
GPIO23: J1.16 (GPIO23), J8.4
GPIO24: J1.18 (GPIO24), J8.3
GPIO25: J1.22 (GPIO25), R2.1
GPIO26: J1.37 (GPIO26), U3.3 (I3)
GPIO27: J1.13 (GPIO27), J8.7
unnamed: C3.1, L1.1, U1.2 (SW)
unnamed: C3.2, U1.6 (VBST)
unnamed: C4.1, C7.1, L1.2, Q11.6 (E), Q12.3 (D), R26.2, R27.2
unnamed: D3.1 (K), R3.1, U3.16 (O1)
unnamed: D3.2 (A), R29.1
unnamed: D4.2 (A), R27.1
unnamed: D5.1 (K), R8.2, U3.15 (O2)
unnamed: D5.2 (A), R30.1
unnamed: D6.1 (K), R12.2, U3.14 (O3)
unnamed: D6.2 (A), R31.1
unnamed: D7.1 (K), R16.2, U3.13 (O4)
unnamed: D7.2 (A), R32.1
unnamed: D8.1 (K), R20.2, U3.12 (O5)
unnamed: D8.2 (A), R33.1
unnamed: D11.2 (A), R1.1
unnamed: D12.2 (A), R6.1
unnamed: D13.2 (A), R10.1
unnamed: D14.2 (A), R14.1
unnamed: D15.1 (K), J15.3, Q2.3 (C)
unnamed: D15.2 (A), R18.1
unnamed: F1.1, Q1.3 (D)
unnamed: J5.2, R3.2
unnamed: J15.4, JP1.2 (C), R18.2
unnamed: J18.2, R8.1
unnamed: J19.2, R12.1
unnamed: J20.2, R16.1
unnamed: J21.2, R20.1
unnamed: J22.1, R19.1, U2.7 (WP)
unnamed: Q2.1 (B), R2.2
unnamed: Q3.1 (B), R5.2
unnamed: Q5.1 (B), R9.2
unnamed: Q7.1 (B), R13.2
unnamed: Q9.1 (B), R17.2
unnamed: Q11.1 (C), Q11.2 (B), Q11.3 (B), R11.2
unnamed: Q11.4 (C), Q12.1 (G), R15.2
unnamed: R23.2, R24.1, SW1.1 (A)
unnamed: R25.2, R26.1, U1.4 (VFB)
unnamed: SW1.2 (B), U1.5 (EN)
ST_BL_2: D1.2 (A), D11.1 (K), J25.2, Q3.3 (C)
ST_BL_4: D2.2 (A), D12.1 (K), J25.4, Q5.3 (C)
ST_BL_6: D9.2 (A), D13.1 (K), J25.6, Q7.3 (C)
ST_BL_8: D10.2 (A), D14.1 (K), J25.8, Q9.3 (C)
ST_TR_1: J26.1, R7.1

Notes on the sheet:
assuming 2v drop, and 5.1v supply. (5.1-2) 20ma > 155ohm 150ohm > 20.66ma 3.27-0.7v, 4.7k 0.5468ma X100 = 54ma max (for led) (assuming 3.27-0.7v, 4.7k ohm, 0.5468ma) if 3.3, 0.5532ma 0.5532 X 5 = 2.766ma 3.27-0.7-0.7, / 2700 = 0.7ma X 5 = 3.5ma 3.3-1.7, / 2700 = 0.6ma X 5 = 3ma
200ma DoorStrike 100X 2ma min at base >>> (3.3-0.7)v, 1.3k ohm (assuming 3.27-0.7v, 1.2k ohm, 2.14ma) if 3.3, 2.17ma 3.3-0.83v, / 510ohm = 4.84ma 3.3-0.83v, / 270ohm = 9.15ma 3.27-0.83v, / 510ohm = 4.784ma X 150 = 717 3.27-0.83v, / 270ohm = 9.037ma X 100 = 903
StrikeStatus -IN NC when Door Closed
LatchStatus -IN NC when Door Closed
ReedSwitchStatus - IN NC when Door Closed
Screw Terminals
MMBT4401 FMMT491TA PMMT491A (up to 1A at aver 200 hfe) 2N222 BC337 S9013 anything that can do > ic 200ma and >100 hfe S1A S1M+ <<<<<< DO-214AC S1M-13-F (DO-214AC) 1N4007
https://webench.ti.com/power-designer/switching-regulator
V 1.2a - fix cap on 1-wire Ver 1.2 - Change Footprint of small toogle switch to include 2 drill - change base resistor from 1.2kΩ o 270Ω for 4 transistors - change led resistors from 1k to 2k - Added reverse polarity protection - move nfc power to drlington array NO!! COM to 5v!! - change some head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
10k pull up resistor and 100nF debounce capacitor
I2C Data
I2C Clock
GPIO consumption LED 3.5ma if 510ohm, 5.04ma X 3 = 15.12 max 700, safe 650 if 270ohm, 9.52ma X 2 = 19.04 max 900 Total 7.106ma 5.04 total = 25.83, new Total = 37.66 under 50ma max 16ma per gpio TPS563210A
5.122V
5.1V Regulator
8.2V - 17V
sw - 0.3A max
Jumper LCSC C5305 LCSCweb https://lcsc.com/product-detail/Shunts-Jumpers_2-54mm-Short-hood_C5305.html MPT 0,5/ 2-2,54 KF128-2.54 (screw terminal 2.54) TE_282834 footprint 4 pin header LCSC C124378 6 pin header LCSC C37208 8 pin header LCSC C190820
2 X 22uf 0805 instead of 47uf https://lcsc.com/product-detail/Multilayer-Ceramic-Capacitors-MLCC-SMD-SMT_SAMSUNG_CL21A226MAQNNNE_22uF-226-20-25V_C45783.html
2.7kΩ
Fuse and Reverse polarity protection
Resistor power 2512 1w 1 2010 3/4w 0.75 1206 1/2w 0.5 1206 1/4w 0.25 0805 1/8w 0.125 0603 1/10w 0.1 0402 1/16w 0.0625 0201 1/20w 0.05
150ma max nfc module 160ma 150x 100X2N222A 1.6ma min at base >>> (3.3-0.7)v, 1.625k ohm (assuming 3.27-0.7v, 1.5k ohm, 1.71ma) if 3.3v, 1.733ma 0.7v voltage drop acorss transistor
Relay4Spare
DoorStrike
DoorBuzzer
Relay3Spare
StatusBuzzer

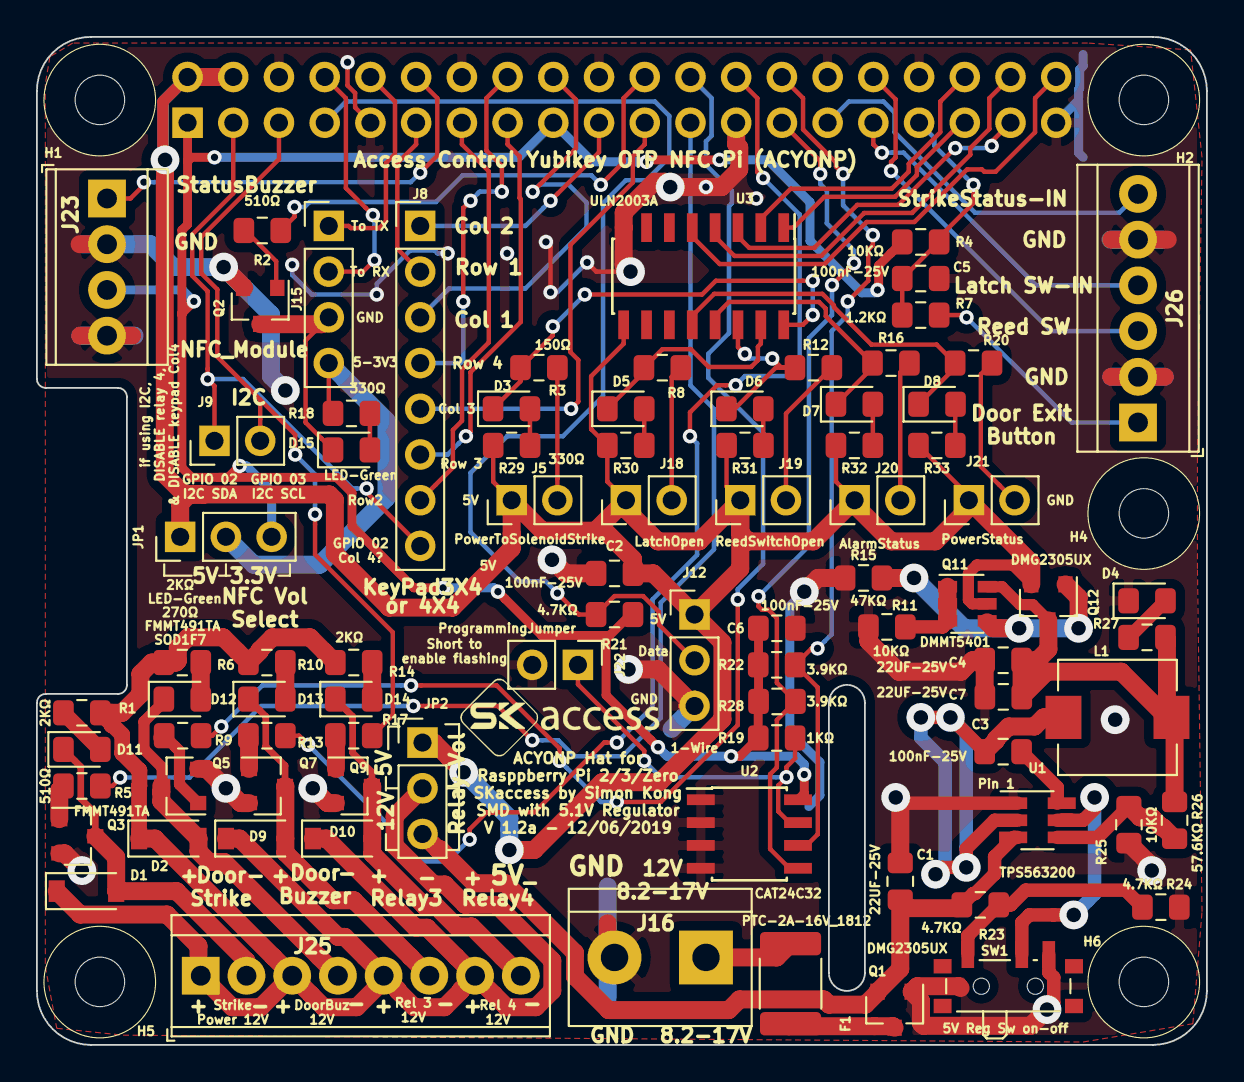
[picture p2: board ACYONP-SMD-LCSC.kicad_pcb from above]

Board: 2 copper layers, 65.0 x 56.0 mm, 91 parts (1 on the bottom side), 77 nets.

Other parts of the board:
H1, H2, H4, H5, H6: MountingHole; MountingHole_2.75mm_M2.5_NoPad

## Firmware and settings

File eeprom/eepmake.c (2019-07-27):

/*
 *	Parses EEPROM text file and createds binary .eep file
 *	Usage: eepmake input_file output_file
*/

#include <stdio.h>
#include <stdlib.h>
#include <ctype.h>
#include <string.h>
#include <stdbool.h>
#include <unistd.h>
#include <fcntl.h>

#include "eeptypes.h"

#define HEADER_SIGN 0x69502d52 //"R-Pi" in ASCII reversed for endianness

//todo: larger initial mallocs

struct header_t header;
struct atom_t *custom_atom, vinf_atom, gpio_atom, dt_atom;
struct vendor_info_d* vinf;
struct gpio_map_d* gpiomap;

bool product_serial_set, product_id_set, product_ver_set, vendor_set, product_set, 
			gpio_drive_set, gpio_slew_set, gpio_hysteresis_set, gpio_power_set;
			
bool data_receive, has_dt, receive_dt;
			
char **data;
char *current_atom; //rearranged to write out
unsigned int data_len, custom_ct, total_size, data_cap, custom_cap;


int write_binary(char* out) {
	FILE *fp;
	int i, offset;
	short crc;
	
	fp=fopen(out, "wb");
	if (!fp) {
		printf("Error writing file %s\n", out);
		return -1;
	}
	
	fwrite(&header, sizeof(header), 1, fp);
		
		
	current_atom = (char *) malloc(vinf_atom.dlen+ATOM_SIZE-CRC_SIZE);
	offset = 0;
	//vendor information atom first part
	memcpy(current_atom, &vinf_atom, ATOM_SIZE-CRC_SIZE);
	offset += ATOM_SIZE-2;
	//data first part
	memcpy(current_atom+offset, vinf_atom.data, VENDOR_SIZE);
	offset += VENDOR_SIZE;	
	//data strings
	memcpy(current_atom+offset, vinf->vstr, vinf->vslen);
	offset += vinf->vslen;
	memcpy(current_atom+offset, vinf->pstr, vinf->pslen);
	offset += vinf->pslen;
	//vinf last part
	crc = getcrc(current_atom, offset);
	memcpy(current_atom+offset, &crc, CRC_SIZE);
	offset += CRC_SIZE;
	
	fwrite(current_atom, offset, 1, fp);
	free(current_atom);
	
	current_atom = (char *) malloc(gpio_atom.dlen+ATOM_SIZE-CRC_SIZE);
	offset = 0;
	//GPIO map first part
	memcpy(current_atom, &gpio_atom, ATOM_SIZE-CRC_SIZE);
	offset += ATOM_SIZE-CRC_SIZE;
	//GPIO data
	memcpy(current_atom+offset, gpiomap, GPIO_SIZE);
	offset += GPIO_SIZE;
	//GPIO map last part
	crc = getcrc(current_atom, offset);
	memcpy(current_atom+offset, &crc, CRC_SIZE);
	offset += CRC_SIZE;
	
	fwrite(current_atom, offset, 1, fp);
	free(current_atom);
	
	if (has_dt) {
		printf("Writing out DT...\n");
		current_atom = (char *) malloc(dt_atom.dlen+ATOM_SIZE-CRC_SIZE);
		offset = 0;
		
		memcpy(current_atom, &dt_atom, ATOM_SIZE-CRC_SIZE);
		offset += ATOM_SIZE-CRC_SIZE;
		
		memcpy(current_atom+offset, dt_atom.data, dt_atom.dlen-CRC_SIZE);
		offset += dt_atom.dlen-CRC_SIZE;
		
		crc = getcrc(current_atom, offset);
		memcpy(current_atom+offset, &crc, CRC_SIZE);
		offset += CRC_SIZE;
		
		fwrite(current_atom, offset, 1, fp);
		free(current_atom);
	}
	
	for (i = 0; i<custom_ct; i++) {
		custom_atom[i].count-=!has_dt;
		
		current_atom = (char *) malloc(custom_atom[i].dlen+ATOM_SIZE-CRC_SIZE);
		offset = 0;
		
		memcpy(current_atom, &custom_atom[i], ATOM_SIZE-CRC_SIZE);
		offset += ATOM_SIZE-CRC_SIZE;
		
		memcpy(current_atom+offset, custom_atom[i].data, custom_atom[i].dlen-CRC_SIZE);
		offset += custom_atom[i].dlen-CRC_SIZE;
		
		crc = getcrc(current_atom, offset);
		memcpy(current_atom+offset, &crc, CRC_SIZE);
		offset += CRC_SIZE;
		
		fwrite(current_atom, offset, 1, fp);
		free(current_atom);
	}
	
	
	fflush(fp);
	fclose(fp);
	return 0;
}


void parse_data(char* c) {
	int k;
	char s;
	char* i = c;
	char* j = c;
	while(*j != '\0')
	{
		*i = *j++;
		if(isxdigit(*i))
			i++;
	}
	*i = '\0';
	
	int len = strlen(c);
	if (len % 2 != 0) {
		printf("Error: data must have an even number of hex digits\n");
	} else {
		for (k = 0; k<len/2; k++) {
			//read a byte at a time
			s = *(c+2);
			*(c+2)='\0';
			
			if (data_len==data_cap) {
				data_cap *=2;
				*data = (char *) realloc(*data, data_cap);
			}
			
			sscanf(c, "%2x", *data+data_len++);
			
			*(c+2) = s;
			c+=2;
		}
	}
}


void finish_data() {
	if (data_receive) {
		*data = (char *) realloc(*data, data_len);
			
		total_size+=ATOM_SIZE+data_len;

		if (receive_dt) {
			dt_atom.type = ATOM_DT_TYPE;
			dt_atom.count = ATOM_DT_NUM;
			dt_atom.dlen = data_len+CRC_SIZE;
		} else {
			//finish atom description
			custom_atom[custom_ct].type = ATOM_CUSTOM_TYPE;
			custom_atom[custom_ct].count = 3+custom_ct;
			custom_atom[custom_ct].dlen = data_len+CRC_SIZE;
			
			custom_ct++;
		}
	}
}


void parse_command(char* cmd, char* c) {
	int val;
	uint32_t high1, high2;
	char *fn, *pull;
	char pin;
	bool valid;
	bool continue_data=false;
	
	/* Vendor info related part */
	if (strcmp(cmd, "product_uuid")==0) {
		product_serial_set = true; //required field
		high1 = 0; high2 = 0;
		
		sscanf(c, "%100s %08x-%04x-%04x-%04x-%04x%08x\n", cmd, &vinf->serial_4, 
			&high1, &vinf->serial_3, &high2, &vinf->serial_2, &vinf->serial_1);
		
		vinf->serial_3 |= high1<<16;
		vinf->serial_2 |= high2<<16;
		
		if ((vinf->serial_4==0) && (vinf->serial_3==0) && (vinf->serial_2==0) && (vinf->serial_1==0)) {
			//read 128 random bits from /dev/urandom
			int random_file = open("/dev/urandom", O_RDONLY);
			ssize_t result = read(random_file, &vinf->serial_1, 16);
			close(random_file);
			if (result <= 0) printf("Unable to read from /dev/urandom to set up UUID");
			else {
				//put in the version
				vinf->serial_3 = (vinf->serial_3 & 0xffff0fff) | 0x00004000;
				
				//put in the variant
				vinf->serial_2 = (vinf->serial_2 & 0x3fffffff) | 0x80000000;
				
				printf("UUID=%08x-%04x-%04x-%04x-%04x%08x\n", vinf->serial_4, vinf->serial_3>>16, vinf->serial_3 & 0xffff, vinf->serial_2>>16, vinf->serial_2 & 0xffff, vinf->serial_1);
			}
 
		}
		
	} else if (strcmp(cmd, "product_id")==0) {
		product_id_set = true; //required field
		sscanf(c, "%100s %hx", cmd, &vinf->pid);
		
	} else if (strcmp(cmd, "product_ver")==0) {
		product_ver_set = true; //required field
		sscanf(c, "%100s %hx", cmd, &vinf->pver);
		
	} else if (strcmp(cmd, "vendor")==0) {
		vendor_set = true; //required field
		
		vinf->vstr = (char*) malloc (256);
		sscanf(c, "%100s \"%255[^\"]\"", cmd, vinf->vstr);
		
		total_size-=vinf->vslen;
		vinf_atom.dlen-=vinf->vslen;
		
		vinf->vslen = strlen(vinf->vstr);
		
		total_size+=vinf->vslen;
		vinf_atom.dlen+=vinf->vslen;
		
	} else if (strcmp(cmd, "product")==0) {
		product_set = true; //required field
		
		vinf->pstr = (char*) malloc (256);
		sscanf(c, "%100s \"%255[^\"]\"", cmd, vinf->pstr);
		
		total_size-=vinf->pslen;
		vinf_atom.dlen-=vinf->pslen;
		
		vinf->pslen = strlen(vinf->pstr);
		
		total_size+=vinf->pslen;
		vinf_atom.dlen+=vinf->pslen;
	} 
	
	/* GPIO map related part */
	else if (strcmp(cmd, "gpio_drive")==0) {
		gpio_drive_set = true; //required field
		
		sscanf(c, "%100s %1x", cmd, &val);
		if (val>8 || val<0) printf("Warning: gpio_drive property in invalid region, using default value instead\n");
		else gpiomap->flags |= val;
		
		
	} else if (strcmp(cmd, "gpio_slew")==0) {
		gpio_slew_set = true; //required field
		
		sscanf(c, "%100s %1x", cmd, &val);
		
		if (val>2 || val<0) printf("Warning: gpio_slew property in invalid region, using default value instead\n");
		else gpiomap->flags |= val<<4;
		
	} else if (strcmp(cmd, "gpio_hysteresis")==0) {
		gpio_hysteresis_set = true; //required field
		
		sscanf(c, "%100s %1x", cmd, &val);
		
		if (val>2 || val<0) printf("Warning: gpio_hysteresis property in invalid region, using default value instead\n");
		else gpiomap->flags |= val<<6;
		
	} else if (strcmp(cmd, "back_power")==0) {
		gpio_power_set = true; //required field
		
		sscanf(c, "%100s %1x", cmd, &val);
		
		if (val>2 || val<0) printf("Warning: back_power property in invalid region, using default value instead\n");
		else gpiomap->power = val;
		
	} else if (strcmp(cmd, "setgpio")==0) {
		fn = (char*) malloc (101);
		pull = (char*) malloc (101);
		
		sscanf(c, "%100s %d %100s %100s", cmd, &val, fn, pull);
		
		if (val<GPIO_MIN || val>=GPIO_COUNT) printf("Error: GPIO number out of bounds\n");
		else {
			valid = true;
			pin = 0;
			
			if (strcmp(fn, "INPUT")==0) {
				//no action
			} else if (strcmp(fn, "OUTPUT")==0) {
				pin |= 1;
			} else if (strcmp(fn, "ALT0")==0) {
				pin |= 4;
			} else if (strcmp(fn, "ALT1")==0) {
				pin |= 5;
			} else if (strcmp(fn, "ALT2")==0) {
				pin |= 6;
			} else if (strcmp(fn, "ALT3")==0) {
				pin |= 7;
			} else if (strcmp(fn, "ALT4")==0) {
				pin |= 3;
			} else if (strcmp(fn, "ALT5")==0) {
				pin |= 2;
			} else {
				printf("Error at setgpio: function type not recognised\n");
				valid=false;
			}
			
			if (strcmp(pull, "DEFAULT")==0) {
				//no action
			} else if (strcmp(pull, "UP")==0) {
				pin |= 1<<5;
			} else if (strcmp(pull, "DOWN")==0) {
				pin |= 2<<5;
			} else if (strcmp(pull, "NONE")==0) {
				pin |= 3<<5;
			} else {
				printf("Error at setgpio: pull type not recognised\n");
				valid=false;
			}
			
			pin |= 1<<7; //board uses this pin
			
			if (valid) gpiomap->pins[val] = pin;
		}
	} 
	
	/* DT atom related part */
	else if (strcmp(cmd, "dt_blob")==0) {
		finish_data();
		
		has_dt = true;
		c+=strlen("dt_blob");
		
		receive_dt=true;
		data_receive=true;
		
		data_len = 0;
		data_cap = 4;
		data = &dt_atom.data;
		*data = (char *) malloc(data_cap);
		
		parse_data(c);
		continue_data = true;
	
	} 
	
	/* Custom data related part */
	else if (strcmp(cmd, "custom_data")==0) {
		finish_data();
		
		c+=strlen("custom_data");
		
		if (custom_cap == custom_ct) {
			custom_cap *= 2;
			custom_atom = (struct atom_t*) realloc(custom_atom, custom_cap * sizeof(struct atom_t));
		}
		
		receive_dt=false;
		data_receive=true;
		
		data_len = 0;
		data_cap = 4;
		data = &custom_atom[custom_ct].data;
		*data = (char *) malloc(data_cap);
		
		parse_data(c);
		continue_data = true;
	
	} else if (strcmp(cmd, "end") ==0) {
		//close last data atom
		continue_data=false;
	}
	/* Incoming data */
	else if (data_receive) {
		parse_data(c);
		continue_data = true;
	} 
	
	
	if (!continue_data) finish_data();
	
}

int read_text(char* in) {
	FILE * fp;
	char * line = NULL;
	char * c = NULL;
	size_t len = 0;
	ssize_t read;
	char *comment = NULL;
	int atomct = 2;
	int linect = 0;
	char * command = (char*) malloc (101);
	int i;
	
	has_dt = false;
	
	printf("Opening file %s for read\n", in);
	
	fp = fopen(in, "r");
	if (fp == NULL) {
		printf("Error opening input file\n");
		return -1;
	}

	//allocating memory and setting up required atoms
	custom_cap = 1;
	custom_atom = (struct atom_t*) malloc(sizeof(struct atom_t) * custom_cap);
	
	total_size=ATOM_SIZE*2+HEADER_SIZE+VENDOR_SIZE+GPIO_SIZE;
	
	vinf_atom.type = ATOM_VENDOR_TYPE;
	vinf_atom.count = ATOM_VENDOR_NUM;
	vinf = (struct vendor_info_d *) calloc(1, sizeof(struct vendor_info_d));
	vinf_atom.data = (char *)vinf;
	vinf_atom.dlen = VENDOR_SIZE + CRC_SIZE;
	
	gpio_atom.type = ATOM_GPIO_TYPE;
	gpio_atom.count = ATOM_GPIO_NUM;
	gpiomap = (struct gpio_map_d *) calloc(1, sizeof(struct gpio_map_d));
	gpio_atom.data = (char *)gpiomap;
	gpio_atom.dlen = GPIO_SIZE + CRC_SIZE;
	
	while ((read = getline(&line, &len, fp)) != -1) {
		linect++;
		c = line;
		
		for (i=0; i<read; i++) if (c[i]=='#') c[i]='\0';
		
		while (isspace(*c)) ++c;
		
		
		if (*c=='\0' || *c=='\n' || *c=='\r') {
			//empty line, do nothing
		} else if (isalnum (*c)) {
			sscanf(c, "%100s", command);
			
#ifdef DEBUG
			printf("Processing line %u: %s", linect, c);
			if ((*(c+strlen(c)-1))!='\n') printf("\n");
#endif
			
			parse_command(command, c);
		
		
		} else printf("Can't parse line %u: %s", linect, c);
	}
	
	finish_data();
	
	if (!product_serial_set || !product_id_set || !product_ver_set || !vendor_set || !product_set || 
			!gpio_drive_set || !gpio_slew_set || !gpio_hysteresis_set || !gpio_power_set) {
			
		printf("Warning: required fields missing in vendor information or GPIO map, using default values\n");
	}
	
	printf("Done reading\n");
	
	return 0;
}


int read_dt(char* in) {
	FILE * fp;
	unsigned long size = 0;
	
	printf("Opening DT file %s for read\n", in);
	
	fp = fopen(in, "r");
	if (fp == NULL) {
		printf("Error opening input file\n");
		return -1;
	}
	
	fseek(fp, 0L, SEEK_END);
	size = ftell(fp);
	fseek(fp, 0L, SEEK_SET);
	
	printf("Adding %lu bytes of DT data\n", size);
	
	total_size+=ATOM_SIZE+size;
	has_dt = true;
	dt_atom.type = ATOM_DT_TYPE;
	dt_atom.count = ATOM_DT_NUM;
	dt_atom.dlen = size+CRC_SIZE;
	
	dt_atom.data = (char *) malloc(size);
	if (!fread(dt_atom.data, size, 1, fp)) goto err;
	
	
	fclose(fp);
	return 0;
	
err:
	printf("Unexpected EOF or error occurred\n");
	fclose(fp);
	return 0;
	
}

int read_custom(char* in) {
	FILE * fp;
	unsigned long size = 0;
	
	printf("Opening custom data file %s for read\n", in);
	
	fp = fopen(in, "r");
	if (fp == NULL) {
		printf("Error opening input file\n");
		return -1;
	}
	
	fseek(fp, 0L, SEEK_END);
	size = ftell(fp);
	fseek(fp, 0L, SEEK_SET);
	
	printf("Adding %lu bytes of custom data\n", size);
	
	total_size+=ATOM_SIZE+size;
	
	custom_atom[custom_ct].type = ATOM_CUSTOM_TYPE;
	custom_atom[custom_ct].count = 3+custom_ct;
	custom_atom[custom_ct].dlen = size+CRC_SIZE;
	
	custom_atom[custom_ct].data = (char *) malloc(size);
	if (!fread(custom_atom[custom_ct].data, size, 1, fp)) goto err;
	
	custom_ct++;
	
	fclose(fp);
	return 0;
	
err:
	printf("Unexpected EOF or error occurred\n");
	fclose(fp);
	return 0;
	
}
int main(int argc, char *argv[]) {
	int ret;
	int i, custom_o=0;
	
	if (argc<3) {
		printf("Wrong input format.\n");
		printf("Try 'eepmake input_file output_file [dt_file] [-c custom_file_1 ... custom_file_n]'\n");
		return 0;
	}
	
	
	ret = read_text(argv[1]);
	if (ret) {
		printf("Error reading and parsing input, aborting\n");
		return 0;
	}
	
	if (argc>3) {
		if (strcmp(argv[3], "-c")==0) {
			custom_o=4;
		} else {
			//DT file specified
			if (dt_atom.dlen) total_size-=(ATOM_SIZE +dt_atom.dlen - CRC_SIZE);
			ret = read_dt(argv[3]);
			if (ret) {
				printf("Error reading DT file, aborting\n");
				return 0;
			}
		}
	}
	
	if (argc>4 && strcmp(argv[4], "-c")==0) custom_o = 5;

	if (custom_o)
		for (i = custom_o; i<argc; i++) {
			//new custom data file
			ret = read_custom(argv[i]);
			if (ret) {
				printf("Error reading DT file, aborting\n");
				return 0;
			}
		}
	
	header.signature = HEADER_SIGN;
	header.ver = FORMAT_VERSION;
	header.res = 0;
	header.numatoms = 2+has_dt+custom_ct;
	header.eeplen = total_size;
	
	printf("Writing out...\n");
	
	ret = write_binary(argv[2]);
	if (ret) {
		printf("Error writing output\n");
		return 0;
	}
	
	printf("Done.\n");

	return 0;
}
